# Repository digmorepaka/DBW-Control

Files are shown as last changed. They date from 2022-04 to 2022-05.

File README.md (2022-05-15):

# Drive by wire controller

## For bench use, testing use, stationary engine use, offroad use, and completely without warranty or liability from me or any of the contributors

## Features:

* UI over Serial
* PID Closed loop control
* Configurable TPS and APP calibration, stored in local EEPROM
* Configurable 3 point Non-linear APP to TPS relation
* EEPROM intergrity checksum
* Multiple throttle states(idle, transient, stable, safety) to improve behavior
* Non-linear 3 point TPS and APP position sensor failure detection
* Semi-automatic failsafe correlation calibration
* Safety mode

## TODO:
* (Off)road test
* Automatic TPS1/TPS2 and APP1/APP2 failsafe correlation calibration
* Increase TPS vs APP configurable cell count
* Voltage compensation
* Improve HW
* Throttle smoothing/delay
* Get to understand parts of the code that I don't undestand :P
* Improve UI, possibly integrate with TunerStudio
* Code cleanup and optimization

## Dependencies:
* frankboesing/FastCRC
* br3ttb/PID
* greygnome/EnableInterrupt
* robtillaart/MultiMap

## Hardware
Designed and ordered a test board

Currently testing with an Arduino UNO and a H bridge. H bridge is configured with a TC4424 driver and a NOT gate as to have a **single direction select pin, and a 5th enable/disable MOSFET**. TC4425/4428 is a better choice because it doesn't needan inverter due to it's mix of inverting/non inverting drivers. This is what I had on hand.

Currently testing with a **Toyota DENSO 89281-52021 Pedal and 22030-0D010 ThrottleBody** from a 2004-2009 Corolla Verso 1ZZ-FE. 2002+ MR2/Celica uses something similar. In the future I will also be working with Kawasaki Versys 1000 2015+ Individual **Mikuni 6307120 throttlebodies**.

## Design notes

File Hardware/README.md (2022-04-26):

# Hardware

## Initial test board

### Goals:
* Completely standalone
* Core stability and safety features
* Fully featured for current software
* Screw terminals
* Easily debugable

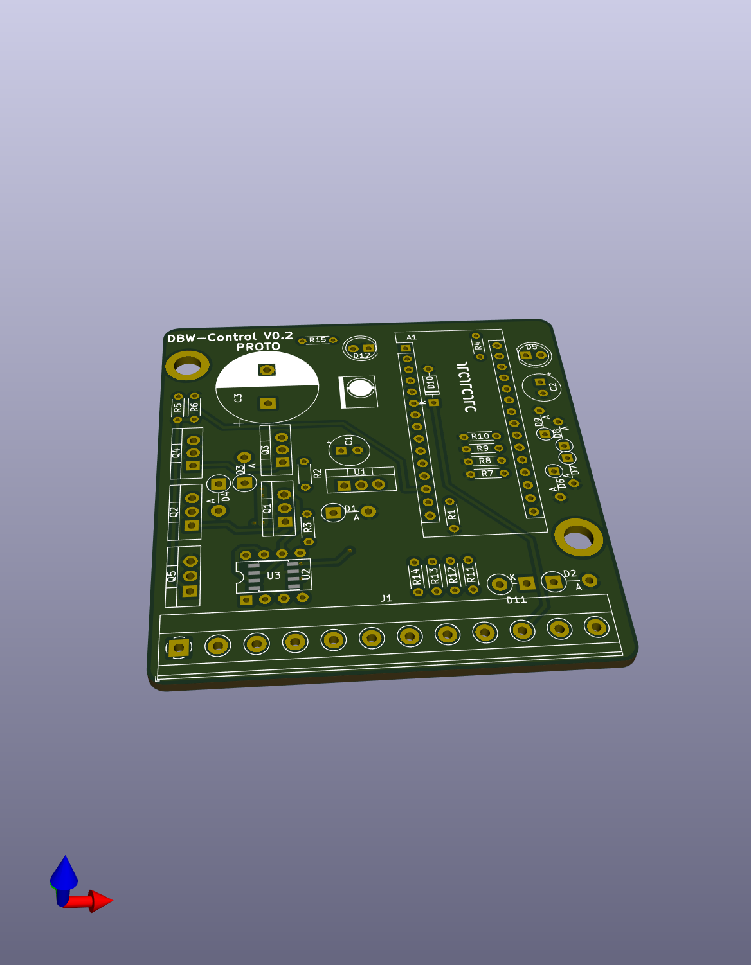
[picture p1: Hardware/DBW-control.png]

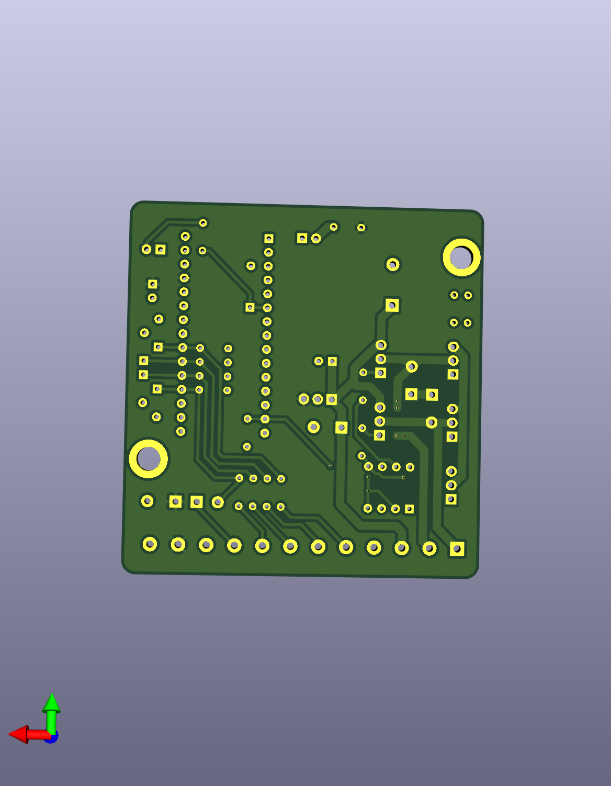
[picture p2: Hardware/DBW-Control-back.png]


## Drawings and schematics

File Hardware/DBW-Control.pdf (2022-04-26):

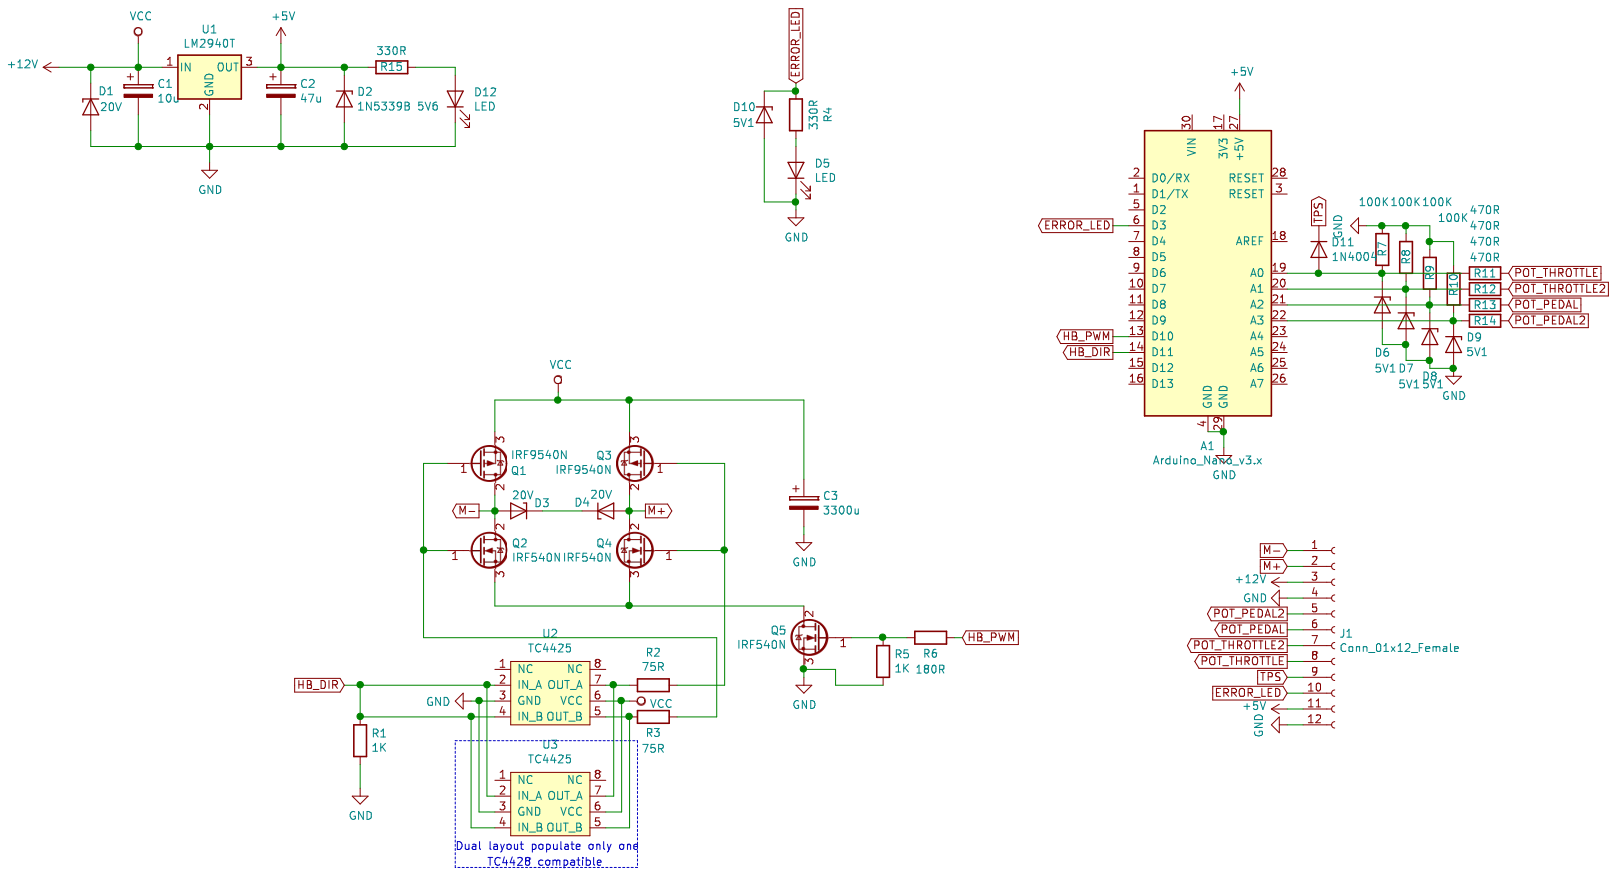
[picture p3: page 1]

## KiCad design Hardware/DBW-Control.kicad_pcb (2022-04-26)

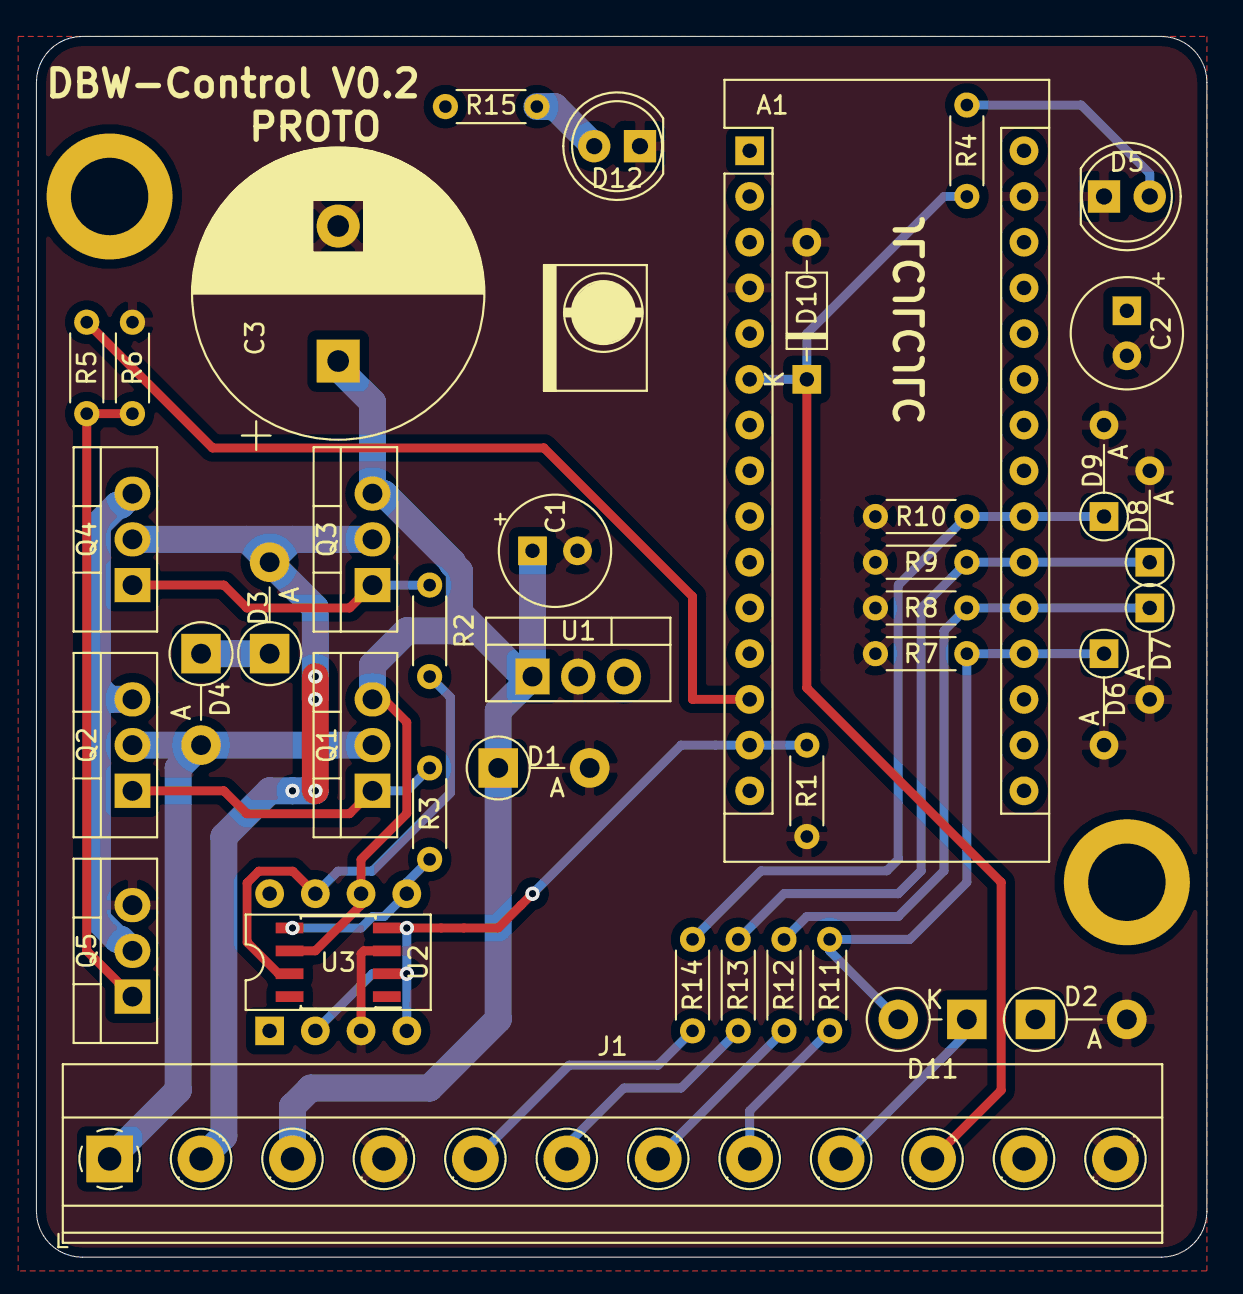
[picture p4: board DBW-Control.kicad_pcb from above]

Board: 2 copper layers, 65.0 x 67.8 mm, 40 parts (0 on the bottom side), 26 nets.

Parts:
A1: Arduino_Nano_v3.x; Arduino_Nano
C1: 10u; CP_Radial_Tantal_D6.0mm_P2.50mm
C2: 47u; CP_Radial_Tantal_D6.0mm_P2.50mm
C3: 3300u; CP_Radial_D16.0mm_P7.50mm
D1, D3, D4: 20V; D_DO-41_SOD81_P5.08mm_Vertical_AnodeUp
D2: 1N5339B 5V6; D_DO-41_SOD81_P5.08mm_Vertical_AnodeUp
D5, D12: LED; LED_D5.0mm
D6, D7, D8, D9: 5V1; D_DO-35_SOD27_P5.08mm_Vertical_AnodeUp
D10: 5V1; D_DO-35_SOD27_P7.62mm_Horizontal
D11: 1N4004; D_DO-41_SOD81_P3.81mm_Vertical_KathodeUp
J1: Conn_01x12_Female; TerminalBlock_Phoenix_MKDS-1,5-12-5.08_1x12_P5.08mm_Horizon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
Q1, Q3: IRF9540N; TO-220-3_Vertical
Q2, Q4, Q5: IRF540N; TO-220-3_Vertical
R1, R5: 1K; R_Axial_DIN0204_L3.6mm_D1.6mm_P5.08mm_Horizontal
R2, R3: 75R; R_Axial_DIN0204_L3.6mm_D1.6mm_P5.08mm_Horizontal
R4, R15: 330R; R_Axial_DIN0204_L3.6mm_D1.6mm_P5.08mm_Horizontal
R6: 180R; R_Axial_DIN0204_L3.6mm_D1.6mm_P5.08mm_Horizontal
R7, R8, R9, R10: 100K; R_Axial_DIN0204_L3.6mm_D1.6mm_P5.08mm_Horizontal
R11, R12, R13, R14: 470R; R_Axial_DIN0204_L3.6mm_D1.6mm_P5.08mm_Horizontal
U1: LM2940T; TO-220-3_Vertical
U2: TC4425; DIP-8_W7.62mm
U3: TC4425; SOIC-8_3.9x4.9mm_P1.27mm

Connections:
+5V: A1.27, C2.1, D2.1, J1.11, R15.1, U1.3
+12V: C1.1, C3.1, D1.1, J1.3, Q1.3, Q3.3, U1.1, U2.6, U3.6
ERROR_LED: A1.6, D10.1, J1.10, R4.2
GND: A1.4, A1.29, C1.2, C2.2, C3.2, D1.2, D2.2, D5.1, D6.2, D7.2, D8.2, D9.2, D10.2, D12.1, J1.4, J1.12, Q5.3, R1.2, R5.2, R7.1, R8.1, R9.1, R10.1, U1.2, U2.3, U3.3
HB_DIR: A1.14, R1.1, U2.2, U2.4, U3.2, U3.4
HB_PWM: A1.13, R6.1
M+: D4.2, J1.2, Q3.2, Q4.2
M-: D3.2, J1.1, Q1.2, Q2.2
unnamed: A1.19, D6.1, D11.2, R7.2, R11.2
unnamed: A1.20, D7.1, R8.2, R12.2
unnamed: A1.21, D8.1, R9.2, R13.2
unnamed: A1.22, D9.1, R10.2, R14.2
unnamed: D3.1, D4.1
unnamed: D5.2, R4.1
unnamed: D12.2, R15.2
unnamed: Q1.1, Q2.1, R3.1
unnamed: Q2.3, Q4.3, Q5.2
unnamed: Q3.1, Q4.1, R2.1
unnamed: Q5.1, R5.1, R6.2
unnamed: R2.2, U2.7, U3.7
unnamed: R3.2, U2.5, U3.5
POT_PEDAL: J1.6, R13.1
POT_PEDAL2: J1.5, R14.1
POT_THROTTLE: J1.8, R11.1
POT_THROTTLE2: J1.7, R12.1
TPS: D11.1, J1.9

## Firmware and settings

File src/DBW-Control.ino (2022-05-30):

#include <FastCRC.h>
#include <FastCRC_tables.h>
#include <FastCRC_cpu.h>
#include <MultiMap.h>
#include <EnableInterrupt.h>
#include <Arduino.h>
#include <PID_v1.h>
#include "ETC.h"


//AlphaX Throttle Control
//Licensed under the GPL v3
/*
Alpha X ThrttoleController
Copyright (C) Norman Paulino

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
You should have received a copy of the GNU General Public License
along with this program; if not, write to the Free Software
Foundation, Inc., 51 Franklin Street, Fifth Floor, Boston, MA  02110-1301, USA.
*/
void loadCalibration();
void serialRead(byte);

// Inputs
const int POT_THROTTLE = A0; // Servo Position Input
const int POT_THROTTLE2 = A1; // Servo Position Input2
const int POT_PEDAL = A3; // Pedal Sensor Input
const int POT_PEDAL2 = A2; // Pedal Sensor Input
const int POT_IDLE = A4; //Requested Idle Input


// Pins H bridge
const byte HB_DIRECTION = 11; // H bridge Direction
const byte HB_PWM = 10;     // H bridge PWM (speed)

// Throttle constraints, max voltages in both direction
 int MinTPS;
 int MinTPS2;
 int HalfTPS2;
 int MaxTPS;
 int MaxTPS2;
 int MaxAPP = 1023;
 int MaxAPP2 = 1023;


 int HalfAPP2;
 int MinAPP = 0;
 int MinAPP2 = 0;
 int inAPP = 0;
 unsigned int throttleRest;
 int calMode = 0;
 int calLevel1 = 0;
 float calVal1 = 0.00;
 int calLevel2 = 0;
 float calVal2 = 0.00;
 int calSuccessCount = 0;
 int calSuccessCountSec = 0;
 int lastTPS2Read = 0;
 int maxTPS2Read = 0;
 int rawTPS2 = 0;
 int rawAPP2 = 0;
 int TPSerror = 0;
 int APPerror = 0;
 int secondAPP2 = 500;
 int secondOutAPP2 = 650;
 int secondTPS2 = 327;
 int secondOutTPS2 = 691;
 int thirdAPP2 = 562;
 int thirdOutAPP2 = 715;
 int thirdTPS2 = 602;
 int thirdOutTPS2 = 1016;

 int tpsPercent = 0;
 int appPercent = 0;

 int expectAPP2 = 0;
 int expectTPS2 = 0;
 
int tenthirdPointAPP;
int tenthirdPointTPS;
float thirdpPointAPPsafety = 0;
float thirdpPointTPSsafety = 0;
float thirdpPointAPP2safety = 0;
float thirdpPointTPS2safety = 0;

float thirdPointAPP = 0;
float thirdPointTPS = 0;
float appIn[] = {0, 0, 0};
float appOut[] = {0, 0, 0};

float app2In[] = {0, 0, 0, 0};
float app2Out[] = {0, 0, 0, 0};

float tps2In[] = {0, 0, 0, 0};
float tps2Out[] = {0, 0, 0, 0};

//PID Control variables
double kP = 2.3;
double kI = 1;
double kD = .9;
//Idle constants
double idlekP = 1.8;
double idlekI = .08;
double idlekD = 0.9;

//customvars
unsigned long timeDiag = 500;
bool diagEnabled = false;
bool calFlag = 0;
int throttleCorr = 0;
int idleSetPoint = 0;
byte throttleMode = 0;
bool safetyCheck = true;
byte safetyCount = 0;
byte safetyMode = 0;

FastCRC8 CRC8;

//Define the PID controller
double Input, Output, SetPoint;
PID throttlePID(&Input, &Output, &SetPoint, kP, kI, kD, DIRECT);
//double idleOutput, idleSetPoint;
//PID idlePID(&Input, &idleOutput,  = true&idleSetPoint, idlekP, idlekI, idlekD, DIRECT);

//Operating States flag 
char state = 's'; //s = safety, t = transient, i = idle, c = constant (steady state)



void setup() {
// put your setup code here, to run once:
 //Enable PID control
 pinMode(3, OUTPUT);
 digitalWrite(3, HIGH);
 Serial.begin(115200);
 Serial.println("Box OK!");
  throttlePID.SetMode(AUTOMATIC);
  throttlePID.SetSampleTime(1);
  //idlePID.SetMode(AUTOMATIC);
  calFlag = EEPROM.read(8);
  if (calFlag){
    uint8_t CRCbuf[37];
    for (int i = 0; i < 38; i++){
      CRCbuf[i] = EEPROM.read(i);
    }
    uint8_t CRCvalue = EEPROM.read(38);
    Serial.print("CRC buffer value = "); Serial.println(CRC8.smbus(CRCbuf, sizeof(CRCbuf)));
    Serial.print("CRC value = "); Serial.println(EEPROM.read(38));
    if (CRCvalue == CRC8.smbus(CRCbuf, sizeof(CRCbuf))){
      loadCalibration();
      Serial.println("Calibration Loaded");
      digitalWrite(3, LOW);
    }
    else{ 
      safetyMode = 3;
      Serial.println("Calibration Corrupted! No loading was done!");
    }
    
  }
  pinMode(HB_DIRECTION, OUTPUT);
  
}

void loop() {
  if (Serial.available()){
    byte serialRead = Serial.read() - 48;
    Serial.println(serialRead);
    serialCommands(serialRead);
  }
  
  //Read all inputs
    int inTPS = analogRead(POT_THROTTLE); //read for example 48, meaning throttle at rest, max is 758
    int rawAPP = analogRead(POT_PEDAL); //read for example 70, app is 0 (no demand), max is 940
  
    int thirdAPP = MaxAPP * thirdPointAPP;
    int thirdTPS = MaxTPS * thirdPointTPS;
    appIn[0] = MinAPP;
    appIn[1] = thirdAPP + MinAPP;
    appIn[2] = MaxAPP;
    appOut[0] = MinTPS;
    appOut[1] = thirdTPS + MinTPS;
    appOut[2] = MaxTPS;
    float sampleSize = 3;

    
    app2In[0] = MinAPP;
    app2In[1] = secondAPP2; //500
    app2In[2] = thirdAPP2; //562
    app2In[3] = MaxAPP; //865
    app2Out[0] = MinAPP2;
    app2Out[1] = secondOutAPP2; //650
    app2Out[2] = thirdOutAPP2; //715
    app2Out[3] = MaxAPP2;

    tps2In[0] = MinTPS; //138
    tps2In[1] = secondTPS2;  //327
    tps2In[2] = thirdTPS2;  //602
    tps2In[3] = MaxTPS; //890
    tps2Out[0] = MinTPS2; //455
    tps2Out[1] = secondOutTPS2; //691
    tps2Out[2] = thirdOutTPS2;  //1016
    tps2Out[3] = MaxTPS2; //1019
    float safeSampleSize = 4;

    appPercent = map(rawAPP, MinAPP, MaxAPP, 0, 100);
    tpsPercent = map(inTPS, MinTPS, MaxTPS, 0, 100);

    idleSetPoint = map(analogRead(POT_IDLE), 0, 835, 0, 250);
    
    switch(throttleMode){
      case 0:
       inAPP = multiMap<float>(rawAPP, appIn, appOut, sampleSize);
       break;
      case 1:
       inAPP = map(rawAPP, MinAPP, MaxAPP, MinTPS, MaxTPS * 0.5);
       break;
    }
    
    if (calMode == 0) {
      if (inAPP <= idleSetPoint){
        state = 'i';  //sets idle mode
      }
      else if (inAPP > idleSetPoint){
        state = 'c'; //Sets to steady state
      }
      if (abs(inTPS - inAPP) >= 60){
        //Serial.println(inTPS -inAPP);
        state = 't';  //sets to transient mode
      }
      if (safetyMode > 0){
        state = 's';
      }
    } else if(calMode > 0) { 
      state = 'k';
      safetyMode = 0;
      safetyCount = 0;
  }

    if (((millis() % 200) == 0) && (safetyCheck == true)){
        rawTPS2 = analogRead(POT_THROTTLE2);
        rawAPP2 = analogRead(POT_PEDAL2);
        expectAPP2 = multiMap<float>(rawAPP, app2In, app2Out, safeSampleSize);
        expectTPS2 = multiMap<float>(inTPS, tps2In, tps2Out, safeSampleSize);
        TPSerror = abs(expectTPS2-rawTPS2);
        APPerror = abs(expectAPP2-rawAPP2);
        
        digitalWrite(3, safetyMode);

        if (state == 'i'){
           TPSerror = 0;
        }
        if ((TPSerror > 10) || (APPerror > 10)){
          safetyCount++;
        }
        else if (safetyCount != 0){
          safetyCount--;
        }
        if (safetyCount == 0){
          state = 'i';
          safetyCheck = true;
          safetyMode = 0;
          throttleMode = 0;
        }
        if(safetyCount > 10){
        //if ((safetyCount > 10) && (safetyCount <= 20)){
          //Serial.println("ETC SYSTEM ERROR!");
          safetyMode = 1;
          throttleMode = 1;
        }
        /*else if ((safetyCount > 20) && (safetyCount <= 30)){
         safetyMode = 2;
          Serial.println("ETC SYSTEM ERROR HIGH!");
        }
        else if (safetyCount > 30){
          safetyMode = 3;
          Serial.println("ETC SYSTEM ERROR CRITICAL!");
        }*/
        safetyCheck = false;
        if ((diagEnabled) && safetyMode > 0){
          Serial.print("TPS Error = "); Serial.println(TPSerror);
          Serial.print("TPS = "); Serial.println(inTPS);
          Serial.print("Expected TPS2  = "); Serial.println(expectTPS2);
          Serial.print("TPS2 = "); Serial.println(rawTPS2);
          Serial.print("APP Error = "); Serial.println(APPerror);
          Serial.print("APP = "); Serial.println(rawAPP);
          Serial.print("Expected APP2  = "); Serial.println(expectAPP2);
          Serial.print("APP2 = "); Serial.println(rawAPP2);
          Serial.print("safetyCount = "); Serial.println(safetyCount);
          Serial.print("safetyMode = "); Serial.println(safetyMode);
          Serial.print(app2In[0]);
          Serial.print(" ");
          Serial.print(app2In[1]);
          Serial.print(" ");
          Serial.print(app2In[2]);
          Serial.print(" ");
          Serial.print(app2In[3]);
          Serial.println(" ");
          Serial.print(app2Out[0]);
          Serial.print(" ");
          Serial.print(app2Out[1]);
          Serial.print(" ");
          Serial.print(app2Out[2]);
          Serial.print(" ");
          Serial.print(app2Out[3]);
          Serial.println(" ");
          Serial.print(tps2In[0]);
          Serial.print(" ");
          Serial.print(tps2In[1]);
          Serial.print(" ");
          Serial.print(tps2In[2]);
          Serial.print(" ");
          Serial.print(tps2In[3]);
          Serial.println(" ");
          Serial.print(tps2Out[0]);
          Serial.print(" ");
          Serial.print(tps2Out[1]);
          Serial.print(" ");
          Serial.print(tps2Out[2]);
          Serial.print(" ");
          Serial.print(tps2Out[3]);
          Serial.println(" ");
          
          /*Serial.print("MaxTPS % = "); Serial.println(MaxTPS);
          Serial.print("MinTPS % = "); Serial.println(MinTPS);
          Serial.print("MaxTPS2 % = "); Serial.println(MaxTPS2);
          Serial.print("MinTPS2 % = "); Serial.println(MinTPS2);
          Serial.print("APPerror = "); Serial.println(APPerror);*/
          
        }
    }
    else if((millis() % 200) != 0) { safetyCheck = true;}
     if ((millis() - timeDiag) > 600){
      if ((diagEnabled) && safetyMode == 0){
        //Serial.print("TPS = "); Serial.println(inTPS);
        Serial.print("Raw APP% = "); Serial.println(appPercent);
        Serial.print("Raw TPS% = "); Serial.println(tpsPercent);
        //Serial.print("Calibrated Target% = "); Serial.println(inappPercent);
        Serial.print("State: "); Serial.println(state);
        Serial.print("Idle = "); Serial.println(idleSetPoint);
        Serial.print("Input idle DC = ");Serial.println(analogRead(POT_IDLE));
        Serial.print("PID Output = "); Serial.println(Output);
        //Serial.print("APP Map In = "); Serial.print(appIn[0]); Serial.print(" "); Serial.print(appIn[1]); Serial.print(" "); Serial.println(appIn[2]);
        //Serial.print("APP Map Out = "); Serial.print(appOut[0]); Serial.print(" "); Serial.print(appOut[1]); Serial.print(" "); Serial.println(appOut[2]);*/
       /* Serial.print("TPS Error = "); Serial.println(TPSerror);
        Serial.print("TPS = "); Serial.println(inTPS);
        Serial.print("Expected TPS2  = "); Serial.println(expectTPS2);
        Serial.print("TPS2 = "); Serial.println(rawTPS2);
        Serial.print("APP Error = "); Serial.println(APPerror);
        Serial.print("APP = "); Serial.println(rawAPP);
        Serial.print("Expected APP2  = "); Serial.println(expectAPP2);
        Serial.print("APP2 = "); Serial.println(rawAPP2);
        Serial.print("safetyCount = "); Serial.println(safetyCount);
        Serial.print("safetyMode = "); Serial.println(safetyMode);
        Serial.print(app2In[0]);
          Serial.print(" ");
          Serial.print(app2In[1]);
          Serial.print(" ");
          Serial.print(app2In[2]);
          Serial.print(" ");
          Serial.print(app2In[3]);
          Serial.println(" ");
          Serial.print(app2Out[0]);
          Serial.print(" ");
          Serial.print(app2Out[1]);
          Serial.print(" ");
          Serial.print(app2Out[2]);
          Serial.print(" ");
          Serial.print(app2Out[3]);
          Serial.println(" ");
          Serial.print(tps2In[0]);
          Serial.print(" ");
          Serial.print(tps2In[1]);
          Serial.print(" ");
          Serial.print(tps2In[2]);
          Serial.print(" ");
          Serial.print(tps2In[3]);
          Serial.println(" ");
          Serial.print(tps2Out[0]);
          Serial.print(" ");
          Serial.print(tps2Out[1]);
          Serial.print(" ");
          Serial.print(tps2Out[2]);
          Serial.print(" ");
          Serial.print(tps2Out[3]);
          Serial.println(" ");*/
      }
      //Serial.print("Idle = "); Serial.println(idleSetPoint);
      timeDiag = millis();
    }
    
   
    //convert inputs to doubles
    Input = inTPS;
    SetPoint = inAPP;
    switch (state){
      case 'c':
      throttlePID.SetTunings(1.1, .07, 0.03);
      //  throttlePID.SetSampleTime(2);
      if (inTPS < inAPP){
          digitalWrite(HB_DIRECTION, 0);            //sets ETC Direction to forward
          throttlePID.SetControllerDirection(DIRECT);
          throttlePID.SetOutputLimits(50,200);
          //Serial.print("PID Output = "); Serial.println(Output);
          throttlePID.Compute();                    //compute PID based correction
          analogWrite(HB_PWM,(Output));  //uses the base duty and adds a correction factor with PID
          //Serial.println("Steady State Forward");
        }
      else {
           digitalWrite(HB_DIRECTION, 1);                       //set ETC Direction Backward
           /*throttlePID.SetTunings(1.4, 1, 0.7);
           throttlePID.SetControllerDirection(REVERSE);
           throttlePID.SetOutputLimits(20,120);
           throttlePID.Compute();   */
           if (abs(inTPS - inAPP) < 5){
            analogWrite(HB_PWM,20);  //makes throttle go backward with open loop values
            //Serial.println("Idle backslow");
           }
           else{
            analogWrite(HB_PWM,80);  //makes throttle go backward with open loop values
            //Serial.println("Idle back");
           }
           throttlePID.Compute();                    //compute PID based correction

          }
      break;
      case 't':
      //Transient function that forces the TP to open at max rate, and close at a relatively fast rate to avoid slamming
      if (inTPS < inAPP && abs(inTPS - inAPP) > 200){ //opening
        digitalWrite(HB_DIRECTION, 0);
        analogWrite(HB_PWM,200);
        //Serial.println("Open Transient");
      } else if(inTPS < inAPP) {
        digitalWrite(HB_DIRECTION, 0);
        analogWrite(HB_PWM,150);
      }
      else {
        digitalWrite(HB_DIRECTION, 1); //closing
          if ((inTPS < throttleRest -50)) {
            analogWrite(HB_PWM, 20);
          //Serial.println("Closing transient - slow");
          }
          else{
            analogWrite(HB_PWM, 170);
            //Serial.println("Closing transient");
          }    
        }
        //Serial.println("Transient mode");
        break;
      case 'i':
        // throttlePID.SetSampleTime(1);
        SetPoint = idleSetPoint;
        if (inTPS < idleSetPoint){
          throttlePID.SetTunings(1.1, .07, 0.0);
          throttlePID.SetControllerDirection(DIRECT);
          digitalWrite(HB_DIRECTION, 0);                //sets ETC Direction to forward
          throttlePID.SetOutputLimits(5,100);
          throttlePID.Compute();                            //compute PID based correction
          analogWrite(HB_PWM,(Output));  //uses the base duty and adds a correction facttor with PID
          //Serial.println("Idle opening");
        }
        else {
          digitalWrite(HB_DIRECTION, 1);                       //set ETC Direction Backward
          /*throttlePID.SetTunings(1.4, 1, 0.7);
          throttlePID.SetControllerDirection(REVERSE);
          throttlePID.SetOutputLimits(20,120);
          throttlePID.Compute();   */
          if (abs(inTPS - idleSetPoint) < 5){
            analogWrite(HB_PWM,20);  //makes throttle go backward with open loop values
            //Serial.println("Idle backslow");
          }
          else{
            analogWrite(HB_PWM,80);  //makes throttle go backward with open loop values
            //Serial.println("Idle back");
          }
          //Serial.println("Idle closing");
          //Serial.println(Output);
          throttlePID.Compute();
        }
        //Serial.println("Idle control");
        break;
      case 's': // safetymodes
        if (safetyMode == 1){ 
          throttlePID.SetTunings(1.9, .07, 0.03);
          SetPoint = constrain(SetPoint, 160, 980);
            
          if (inTPS < inAPP){
            digitalWrite(HB_DIRECTION, 0);            //sets ETC Direction to forward
            throttlePID.SetControllerDirection(DIRECT);
            throttlePID.SetOutputLimits(20,180);
            //Serial.print("PID Output = "); Serial.println(Output);
            throttlePID.Compute();                    //compute PID based correction
            analogWrite(HB_PWM,(Output));  //uses the base duty and adds a correction factor with PID
            //Serial.println("Steady State Forward");
          }
          else {
            digitalWrite(HB_DIRECTION, 1);                       //set ETC Direction Backward
            /*throttlePID.SetTunings(1.4, 1, 0.7);
            throttlePID.SetControllerDirection(REVERSE);
            throttlePID.SetOutputLimits(20,120);
            throttlePID.Compute();   */
            if (abs(inTPS - inAPP) < 5){
              analogWrite(HB_PWM,20);  //makes throttle go backward with open loop values
              //Serial.println("Idle backslow");
            }
            else{
              analogWrite(HB_PWM,80);  //makes throttle go backward with open loop values
              //Serial.println("Idle back");
            }
            throttlePID.Compute();                    //compute PID based correction
  
          }
        }
        else if (safetyMode == 2){
          digitalWrite(HB_DIRECTION, 1);
          analogWrite(HB_PWM,60);
        }
        else {
          digitalWrite(HB_DIRECTION, 1);
          analogWrite(HB_PWM,0);
          safetyCheck = false;
        }
        break;
      case 'k': //calibration mode
        switch(calMode){
          case 1:
            switch(calSuccessCountSec){
            case 0:
              switch(calSuccessCount){
                case 0:
                  SetPoint = calLevel1;
                  break;
                case 1:
                  SetPoint = calLevel2;
                  break;
              }
              break;
            case 1:
              break;
            }


            throttlePID.SetTunings(1.3, .07, 0.02);
            if (abs(SetPoint - inTPS) > 40){
              if (inTPS < SetPoint){ //opening
                digitalWrite(HB_DIRECTION, 0);
                analogWrite(HB_PWM,220);
                //Serial.println("Open Transient");
              }
              if(inTPS > SetPoint){
                digitalWrite(HB_DIRECTION, 1);
                analogWrite(HB_PWM,50);
              }     
              
            } else if (inTPS < SetPoint){
              digitalWrite(HB_DIRECTION, 0);            //sets ETC Direction to forward
              throttlePID.SetControllerDirection(DIRECT);
              throttlePID.SetOutputLimits(20,230);
              throttlePID.Compute();                    //compute PID based correction
              analogWrite(HB_PWM,(Output));  //uses the base duty and adds a correction factor with PID
                  
            }
            else {
              digitalWrite(HB_DIRECTION, 1);                       //set ETC Direction Backward
              /*throttlePID.SetTunings(1.4, 1, 0.7);
              throttlePID.SetControllerDirection(REVERSE);
              throttlePID.SetOutputLimits(20,120);
              throttlePID.Compute();   */
              if (abs(inTPS - SetPoint) < 5){
                analogWrite(HB_PWM,5);  //makes throttle go backward with open loop values
                //Serial.println("Idle backslow");
              }
              else{
                analogWrite(HB_PWM,20);  //makes throttle go backward with open loop values
                //Serial.println("Idle back");
              }
              throttlePID.Compute();                    //compute PID based correction
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

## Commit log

2022-04-26 Add Initial hardware
    [DBW-Control.kicad_pcb, DBW-Control.sch]
2022-05-11 Automatic calibration

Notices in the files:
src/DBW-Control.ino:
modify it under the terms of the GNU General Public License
